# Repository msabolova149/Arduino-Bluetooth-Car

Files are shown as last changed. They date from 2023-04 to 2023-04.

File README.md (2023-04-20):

# Arduino Bluetooth Robot

In this school project I made a bluetooth controlled robot using Arduino. 
Usually, remote-controlled robots are controlled by RC remotes, but I chose an android phone.
For this project, I also created a case with a 3D printer and designed it in OpenScad program.

See in 3D : [show](Bluetooth_robot_with_all_parts.stl)

### Case

Parts of the 3D case:
* [head](head.stl)
* [upper part](upper_part.stl)
* [lower part](lower_part.stl)

A 3D robot with some parts can be seen in Bluetooth_robot_with_all_parts.stl.
To write and upload code to the Arduino boards is used Arduino IDE program (variant of the C++ programming language).

Robot moves forward, backward, right and left. It has lights and buzzes at distance less than 30 cm.

### List of hardware components:
* [Arduino UNO (board)](https://techfun.sk/produkt/arduino-uno-smd-edicia-precizny-klon/)
* [Motor driver shield](https://techfun.sk/produkt/motor-driver-shield-l293d/)
* [2 - DC Motors with Wheels](https://techfun.sk/produkt/dc-motorcek-pneumatika/)
* [Smart car wheel (passive)](https://techfun.sk/produkt/otocne-koliesko-pre-stavebnice-auticok/)
* [HC-06 Bluetooth Module](https://techfun.sk/produkt/bluetooth-modul-hc-06-slave/)
* 2 - Li-ion Batteries OR 9V Battery
* [Switcher](https://techfun.sk/produkt/jednoduchy-prepinac/)
* Jumper wires (various types)
* Double sided tape or glue, screws, screwdriver

#### Optional:
* [2 - LED RGB modules](https://techfun.sk/produkt/led-rgb-modul/) OR 2 - RGB leds + 6 - resistors (3 for 1 led)
* [PCB](https://techfun.sk/produkt/nepajive-pole-170-bodov/)
* [Ultrasonic sensor](https://techfun.sk/produkt/ultrazvukovy-senzor-vzdialenosti-hy-srf05/)
* [Buzzer](https://techfun.sk/produkt/pasivny-buzzer-samostatne/)

### Step 1
Soldering wires to motors and attaching it under the lower part of case with tape or glue.
Connecting wheels to robot. 

### Step 2
Connecting Arduino Uno and motor driver shield together. Then placing it on upper part of case.

### Step 3
Mounting the battery pack + soldering wires to switcher, attaching it in the lower part of case.

### Step 4
Mounting the HC-06 module.

#### Optional step
*Mounting led RGB modules, ultrasonic sensor and buzzer via board to motor shield.
Ultrasonic sensor belongs to the head part of case, the other components to the lower part.*

### Step 5
Connection of all components according to the wiring diagram. [diagram](wiring_diagram.png)

### Step 6
Programming the Arduino Uno board with Arduino IDE.

### Step 7
Downloading the Android App from Google Play Store.
* [Bluetooth RC Car](https://play.google.com/store/apps/details?id=braulio.calle.bluetoothRCcontroller) (suggestion)

### Step 8
Code

*Note: Before uploading the sketch on the Uno board, it is neccesary to remove two jumper wires that is connected to the TX and RX pin of Arduino. Otherwise Arduino IDE gives us a programming error. After successfully uploading the sketch, connect the two wires (TX and RX) on their places.*

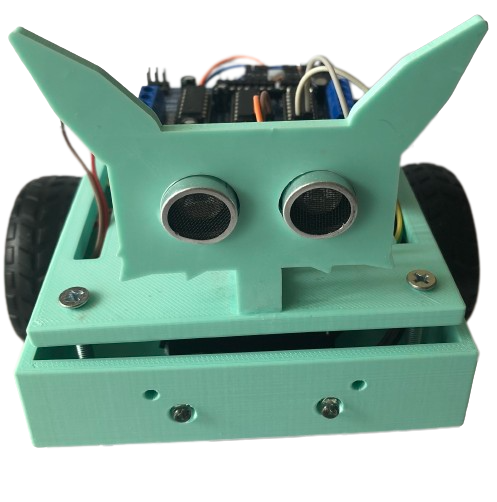
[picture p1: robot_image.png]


### Program for movements:

``` c++
#include <AFMotor.h>

AF_DCMotor motor1(1); 
AF_DCMotor motor2(4);
char command; 

void setup() {       
  Serial.begin(9600);  
}

void loop(){
    if(Serial.available() > 0){ 
          command = Serial.read(); 
          Stop();
      
          switch(command){
          case 'F':  
            forward();
            break;
          
          case 'B':  
            back();
            break;
          
          case 'L':  
            left();
            break;
          
          case 'R':
            right();
            break;
          }
    }
} 

void forward(){
  motor1.setSpeed(255); 
  motor1.run(FORWARD); 
  
  motor2.setSpeed(255);
  motor2.run(FORWARD);
}

void back(){ 
  motor1.setSpeed(255); 
  motor1.run(BACKWARD); 
  
  motor2.setSpeed(255); 
  motor2.run(BACKWARD); 
}

void left(){
  motor1.setSpeed(255); 
  motor1.run(BACKWARD); 
  
  motor2.setSpeed(255); 
  motor2.run(FORWARD);  

}

void right(){
  motor1.setSpeed(255); 
  motor1.run(FORWARD); 
  
  motor2.setSpeed(255); 
  motor2.run(BACKWARD); 

} 

void Stop(){
  motor1.setSpeed(0); 
  motor1.run(RELEASE); 
  
  motor2.setSpeed(0); 
  motor2.run(RELEASE); 
}
```

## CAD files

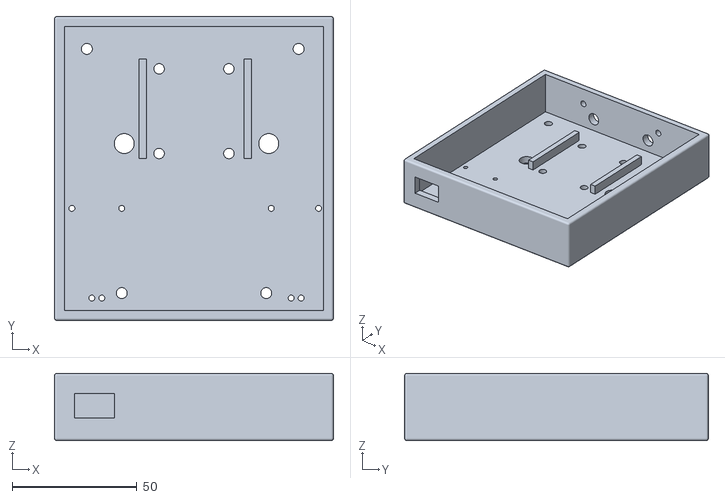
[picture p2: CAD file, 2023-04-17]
lower_part.stl
112.0 x 122.0 x 27.0

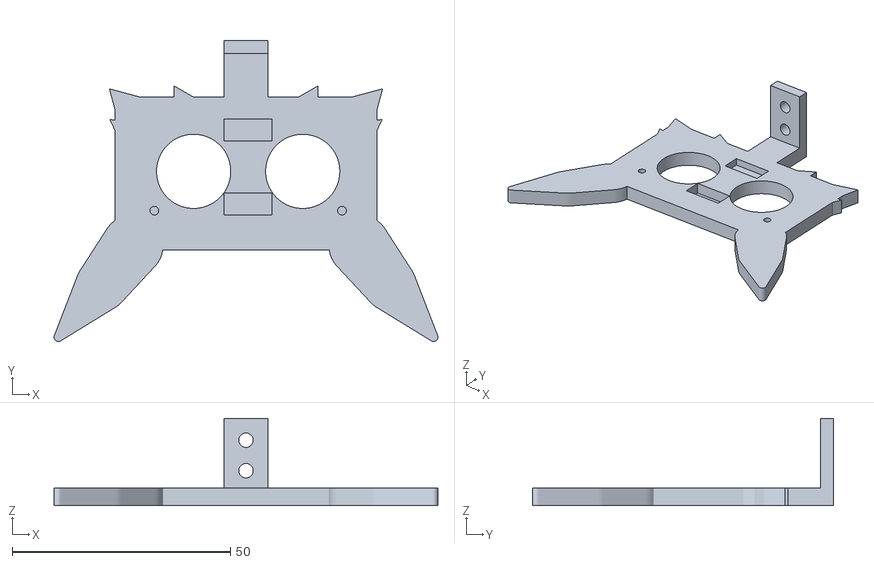
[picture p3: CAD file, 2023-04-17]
head.stl
88.0 x 69.0 x 20.0

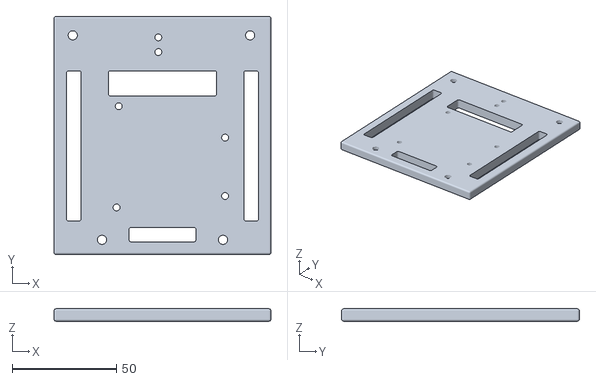
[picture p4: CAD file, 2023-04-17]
upper_part.stl
104.0 x 114.0 x 6.00

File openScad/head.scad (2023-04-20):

$fn = 80;

hr = 4;
move_by = 25;
s = 60;
d = 35;
r2 = 3.3/2;

union(){
	difference(){  
		translate([move_by,move_by+10,0]) cube([s,d,hr]);

		// eyes
		translate([43, 53, -3]) cylinder(h = 17, r = 8.5); 
		translate([68, 53, -3]) cylinder(h = 17, r = 8.5);    

		//screws
		translate([34, 44, 1]) cylinder(h = 10, r = 1);
		translate([77, 44, 1]) cylinder(h = 10, r = 1);   

		// cuts
		translate([50, 43, 1]) cube([11, 5, 12]);
		translate([50, 60, 2]) cube([11, 5, 12]);

	} // diff


	rotate([0,0,25])translate([50, 47,0]) cylinder(h = hr, r = 2,$fn=3);
	rotate([0,0,15]) translate([44, 59,0]) cylinder(h = hr, r = 5,$fn=3);

	translate([110,0,0])
		mirror([1,0,0]){
			rotate([0,0,25]) translate([50, 47,0]) cylinder(h = hr, r = 2,$fn=3);
			rotate([0,0,15]) translate([44, 59,0]) cylinder(h = hr, r = 5,$fn=3);
		}// mir

	translate([40, 70,0]) cylinder(h = hr, r = 3,$fn=3);
	mirror([1,0,0])  translate([-70, 70, 0]) cylinder(h = hr, r = 3,$fn=3);

	// ears
		hull(){
			translate([12,15,0]) cylinder(r=1, h =hr);
			translate([22,27,0]) cylinder(r=6, h =hr);
			translate([29,36,0]) cylinder(r=7, h =hr);
		}

		translate([110,0,0]) mirror([1,0,0])
		hull(){
			translate([12,15,0]) cylinder(r=1, h =hr);
			translate([22,27,0]) cylinder(r=6, h =hr);
			translate([29,36,0]) cylinder(r=7, h =hr);
		}
	// neck
		translate([50, 70,0]) cube([10, 10, hr]);

		difference(){
			translate([50, 80,0]) cube([10, 3, 20]);
			// 	
			rotate([90,0,0]) translate([55, 15,-87]) cylinder(h = 10, r =r2);
			rotate([90,0,0]) translate([55, 8,-87]) cylinder(h = 10, r =r2);
		}
} // u

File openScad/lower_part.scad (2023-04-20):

$fn = 80;

width = 110;
lenght = 120;
v_s = 25; // s

o_kol = 2.1; //mm r
motor = 10;// v
led = 3.3; // rgb
mm = 86;

rr = 2.2; //screw

union(){
    difference(){
        minkowski(){
            sphere(1);
        cube([width, lenght, v_s]);
        }// 
        translate([3,3,3]) cube([width-6, lenght-6, v_s+10]);
            
		// motors
		translate([14,8,-5])  cylinder(h = 20, r = 1.2);
	   translate([18,8,-5]) cylinder(h = 20, r = 1.2);       
	   translate([8+mm,8,-5])  cylinder(h = 20, r = 1.2);
	   translate([12+mm,8,-5]) cylinder(h = 20, r = 1.2);  
	  
	   
	   translate([6,44,-15]) cylinder(h = 30, r = 1.2);
	   translate([26,44,-15])  cylinder(h = 30, r = 1.2);  
	   translate([mm,44,-15]) cylinder(h = 30, r = 1.2);
	   translate([19+mm,44,-15]) cylinder(h = 30, r = 1.2);
		
	   // gear wire
	   translate([85,70,-5]) cylinder(h = 20, r = 4);
	   translate([27,70,-5])  cylinder(h = 20, r = 4);
		
		// for switcher
		translate([7,-5,8])cube([16, 15, 10]);
		
		// for rgb leds
		rotate([90, 0,0]) translate([width/3-1,10,-lenght-10]) cylinder(h = 30, r = led);

		rotate([90, 0,0])translate([width/3-8,17,-lenght-10]) cylinder(h = 30, r = 1.7);   
		rotate([90, 0,0]) translate([2*width/3-1,10,-lenght-10]) cylinder(h = 30, r = led);
		rotate([90, 0,0]) translate([2*width/3+6,17,-lenght-10]) cylinder(h = 30, r = 1.7);
		
		
		// passive wheel
		translate([33+8,lenght -20,-2]) cylinder(h = 10, r = o_kol);
		translate([33+8,lenght -20- 34,-2]) cylinder(h = 10, r = o_kol);
		translate([33 + 28+8,lenght -20,-2]) cylinder(h = 10, r = o_kol);     
		translate([33 + 28+8,lenght -20 -34,-2]) cylinder(h = 10, r = o_kol);
		
		// screws
		translate([12, lenght-12, -8]) cylinder(h= 30, r = rr);
		translate([12+85, lenght-12, -8]) cylinder(h= 30, r = rr);
		translate([26, 10, -8]) cylinder(h= 30, r = rr);
		translate([84, 10, -8]) cylinder(h= 30, r = rr);
    
    }       // d
      
// board
    translate([33,64,3]) cube([3, 40, 5]); 
    translate([75,64,3]) cube([3, 40, 5]); 

} // 

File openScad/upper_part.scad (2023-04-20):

$fn = 80;

width = 110;
height = 120;
rr = 2.2;  //screw
r3 = 3.3/2;

union(){
    
    difference(){
		translate([4,4,0])
			minkowski(){
				sphere(1);
			cube([width-8, height-8, 4]);
			}// 
		// screws
		translate([12, height-12,-2]) cylinder(h= 10, r = rr);
		translate([12+85, height-12, -2]) cylinder(h= 10, r = rr);
		translate([26, 10, -2]) cylinder(h= 10, r = rr);
		translate([84, 10, -2]) cylinder(h= 10, r = rr);
		
		translate([30, 80, -2])
			minkowski(){
					sphere(1);
				cube([50,10, 15]);
			}
		
		translate([40, 10, -2])
			minkowski(){
				sphere(1);
				cube([30,5, 15]);
		}
    // 
		translate([95, 20, -2])
			minkowski(){
				sphere(1);
				cube([5,70, 10]);
		}
		translate([10, 20, -2])
			minkowski(){
				sphere(1);
				cube([5,70, 10]);
		}
    
    // for arduino
		translate([33, 25.5,-2]) cylinder(h= 15, r = r3);
		translate([34, 74,-2]) cylinder(h= 15, r = r3);
		translate([85, 31,-2]) cylinder(h= 15, r = r3);
		translate([85, 59,-2]) cylinder(h= 15, r = r3);
    
		// for head
		translate([53, 100,-2]) cylinder(h= 15, r = r3);
		translate([53, 107,-2]) cylinder(h= 15, r = r3);
    
	} // d
      
} // u

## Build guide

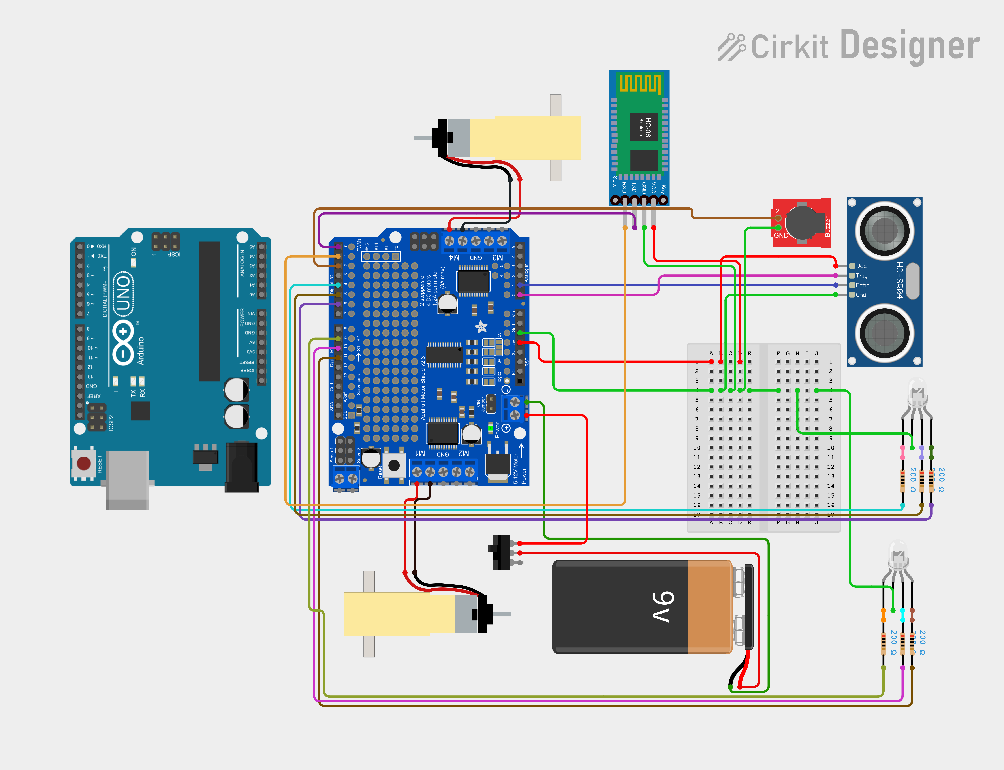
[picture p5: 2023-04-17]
wiring_diagram.png

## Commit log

2023-04-17 .stl files for 3D printing
    [head.stl, lower_part.stl, upper_part.stl]
2023-04-17 wiring diagram image
2023-04-20 arduino IDE
2023-04-20 .scad 3D parts for editing
    [head.scad, lower_part.scad, upper_part.scad]
